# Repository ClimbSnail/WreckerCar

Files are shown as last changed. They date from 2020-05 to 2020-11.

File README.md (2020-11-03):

## 机械臂清障车介绍
本作品参加2017年12月中日韩创新工程竞赛，获金奖（大三上参加的）



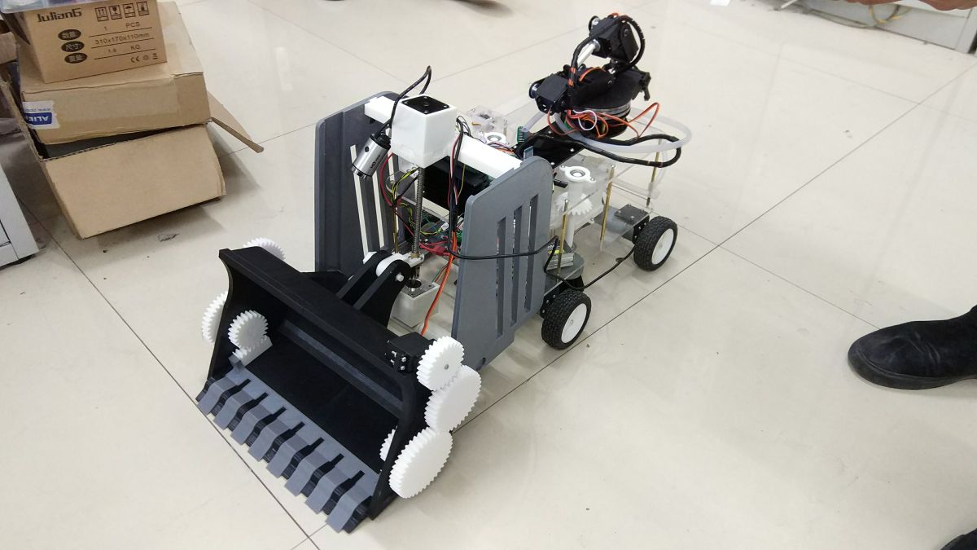
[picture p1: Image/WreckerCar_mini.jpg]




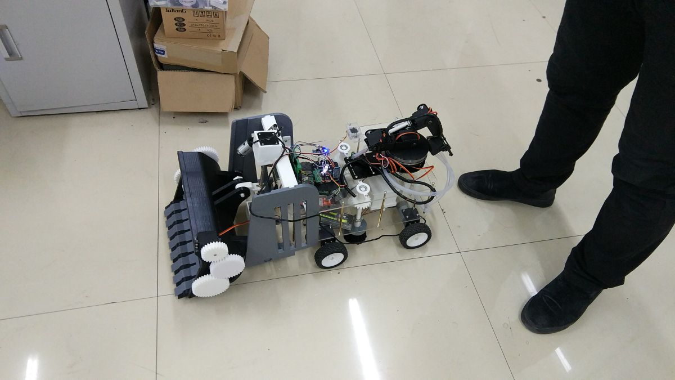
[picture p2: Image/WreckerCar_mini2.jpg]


B站视频[链接](https://b23.tv/BV1qs411L7e6) https://b23.tv/BV1qs411L7e6

如用于学习，可自行去STC官网下载STC12系列的芯片手册。

### 作品简介
1. 电路板:电路图的设计，pcb板的绘制都是由我们自行完成，交由专业厂家打烊，制作成如今的成品。整个作品电源降压、升压部分也特别多，也是一个大工程。

2. 使用价格低廉的51系列主控，对硬件合理的分配及算法的优化，最大程度的挖掘硬件的性能。

3. 控制:使用手机端的app连接机械臂清障车的蓝牙，通过手机蓝牙给控制板发送指令，使之执行特定的动作。

4. 机械臂:使用模拟的六路pwm，并作用独特的联动算法，所有舵机的角度由程序自动计算然后分配，无需人工，使得控制机械臂的时候变得十分简单。

5. 主控控制步进升降:为了增强步进电机的扭力，使用了步进电机驱动器。主控芯片给步进电机驱动器一定的脉冲，从而使信号放大驱动步进电机。

6. 车轮:使用pwm信号并使用光耦隔离驱动多mos管输出大电流以保证底盘四个555电机的正常工作。程序中内置加速减速控制，可实时调车速，保证不同路况的安全运行。使用左右轮差速的方案使得车体在最小的空间中也能完成转向。

7. 水泵和扫帚:使用类似车轮的控制mos管的方案驱动水泵或减速电机。（可调速控制）

8. 车体测边的垃圾箱:使用一个舵机控制车体侧边的垃圾箱收放。

9. 铲斗使用一个舵机完成前后来回铲。

10. 红外功能:为保证安全，车前装有一个红外传感器，当前方有墙之类的障碍使系统自动让车体制动，避免发生意外。

11. LED灯:为适应清障车夜间工作，额外添加了大功率led灯，此led可以实时调整亮度。

12. 远程图像回传摄像头:通过对普通路由器的改装，并刷入基于linux系统的openwrt系统，使日常电脑用的摄像头能够连接路由器，并且使用电脑或者手机浏览器登入查看实时监控。（登入地址http://192.168.1.1:8080/?action=stream）

#### 文件结构
* WreckerCarPCB_Project _（清障车的电路工程文件 AD17绘制）_
* WreckerCar_Code _（清障车的51控制代码 MDK5工程）_
* StructuralDraw _（清障车的solidwork2016结构工程）_
* Image _（实物图片）_
* 多功能消防清障车说明书.doc _（中日韩2017比赛时提交的作品说明书）_
	
#### PCB 3D预览图



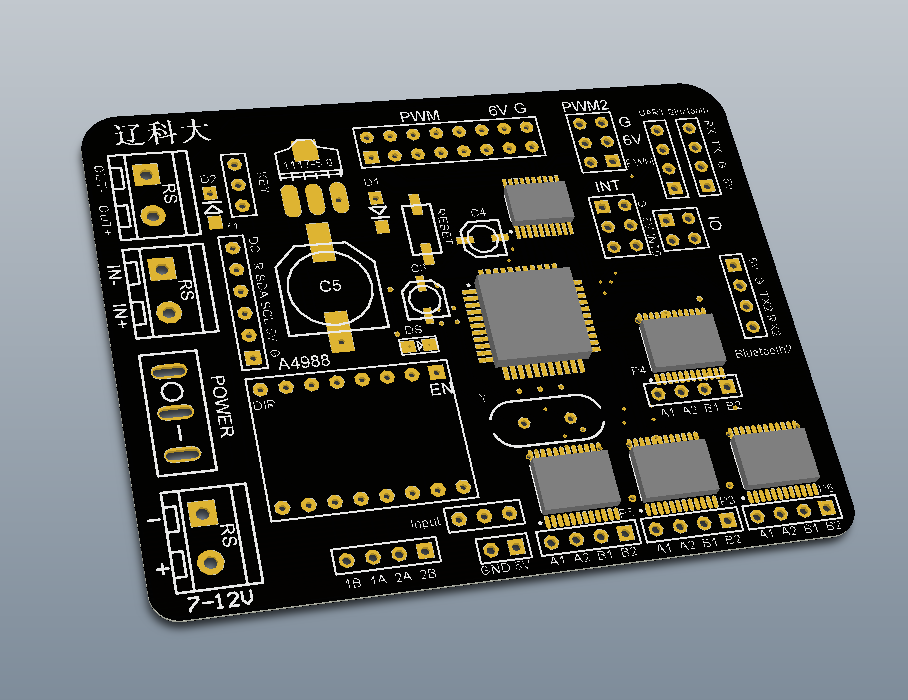
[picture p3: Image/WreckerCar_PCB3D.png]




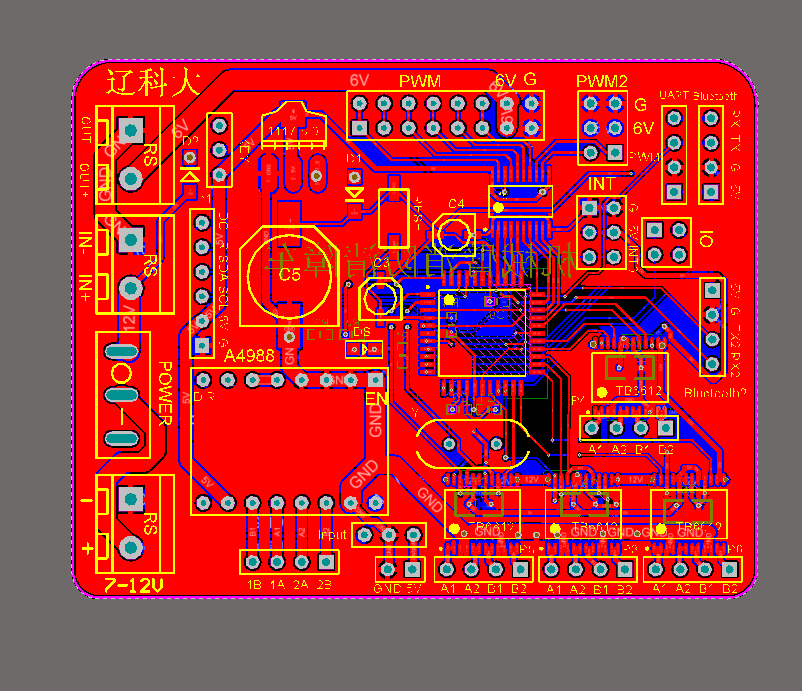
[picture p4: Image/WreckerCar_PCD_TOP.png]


#### 电路存在的问题
	1. 车轮使用的是四个555电机，TB6612不足以驱动（一片TB6612驱一个555时供电不到3s TB6612烧炸）
	2. 由于电机驱动问题，最后另外买了网上现成的驱动板（不用板载的TB6612驱动）。
	3. 铲斗用的步进驱动从原来的A4988改为了TB6600驱动器。

#### 关于代码问题
	1. 之前预计着添加OLED屏幕，调试的过程中烧坏了，最终决定舍弃。

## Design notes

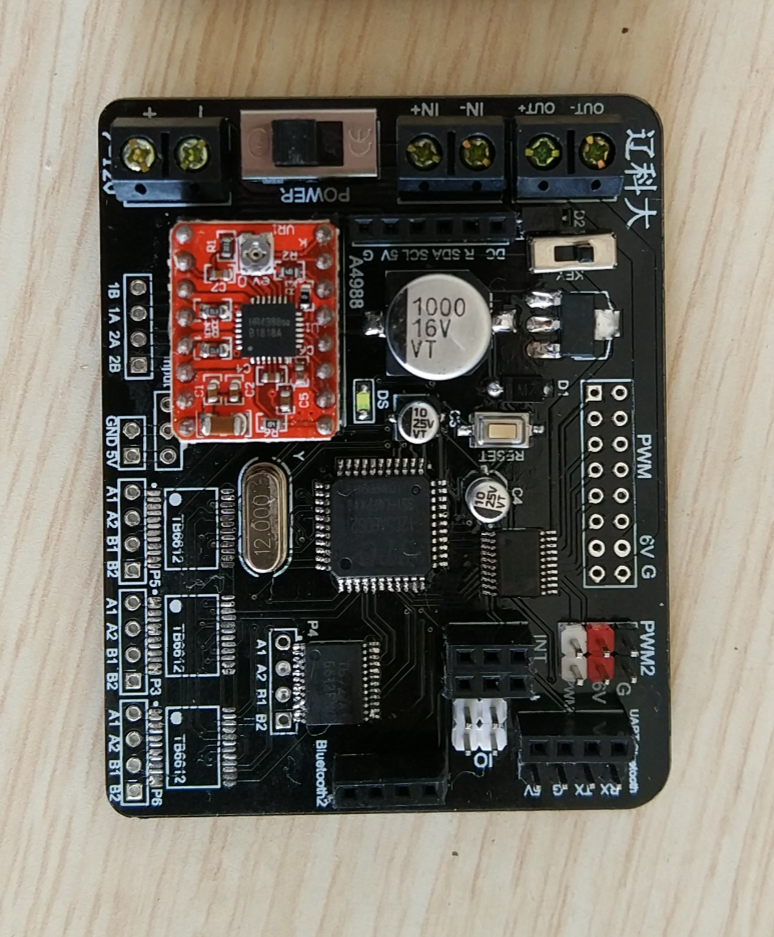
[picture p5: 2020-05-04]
Image/QQ截图20171221224418.png

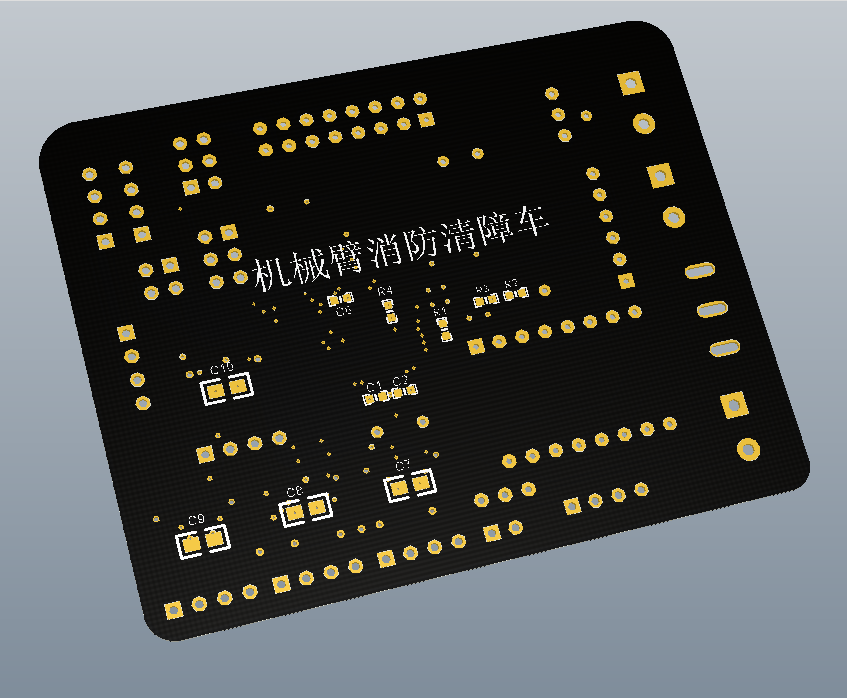
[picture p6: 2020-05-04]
Image/WreckerCar_PCB3D_R.png

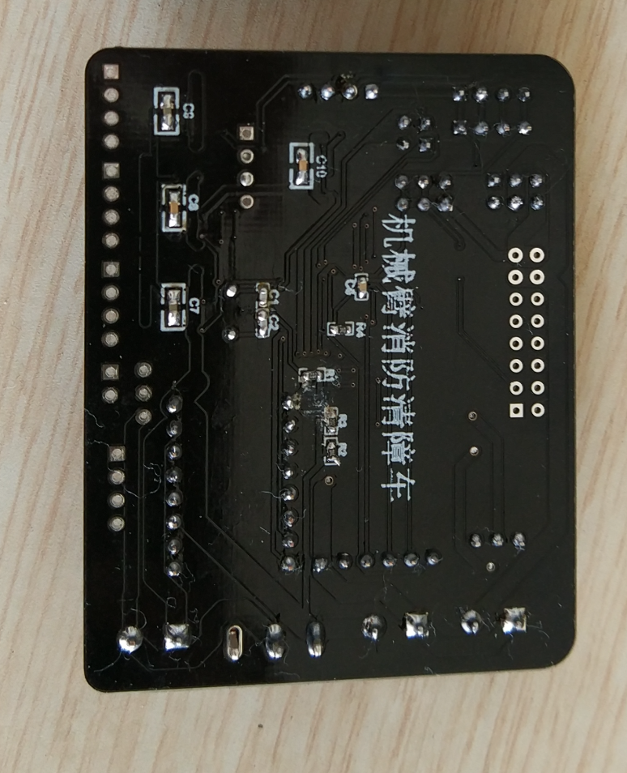
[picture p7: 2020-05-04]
Image/QQ截图20171221224447.png

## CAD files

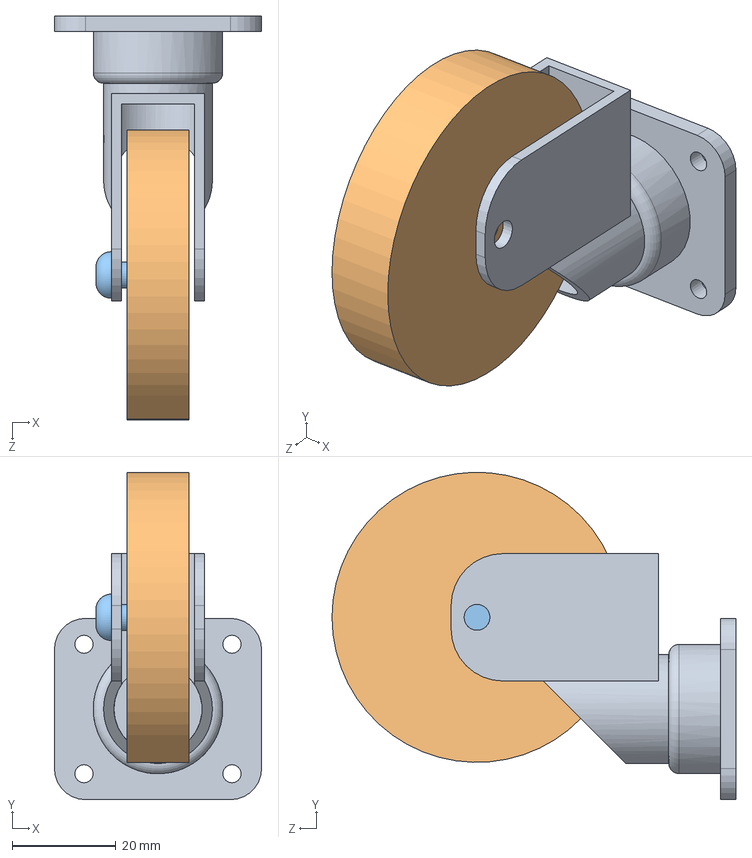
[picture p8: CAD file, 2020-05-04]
StructuralDraw/万向轮/装体123.SLDASM
40.0 x 63.2 x 78.0 mm

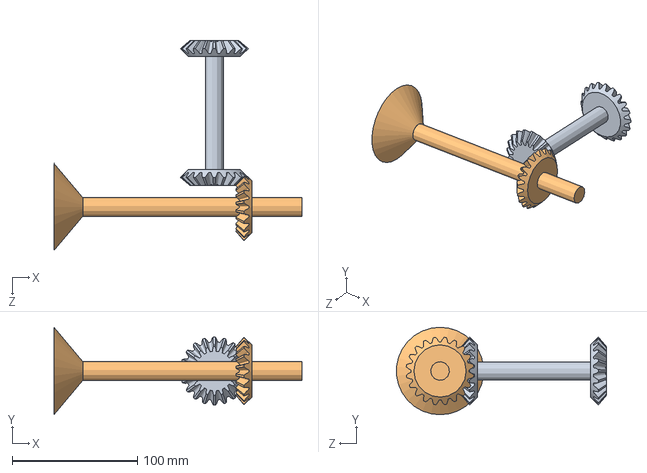
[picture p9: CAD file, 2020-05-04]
StructuralDraw/清洁机构/锥齿轮装配.SLDASM
198.0 x 69.8 x 167.6 mm
锥齿轮01
清洁杆

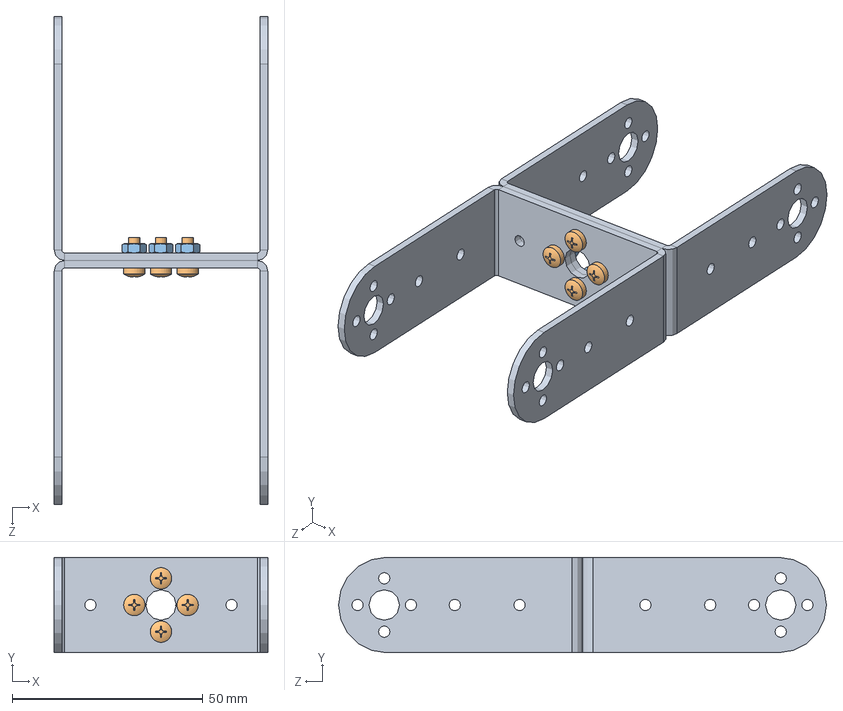
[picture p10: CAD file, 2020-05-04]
StructuralDraw/简易机械臂新底板/长臂组合.SLDASM
56.0 x 25.0 x 128.0 mm
JXS005 x 2
GB818-M3X8-ZN-4.8 x 4
GB6170-M3-ZN-10 x 4

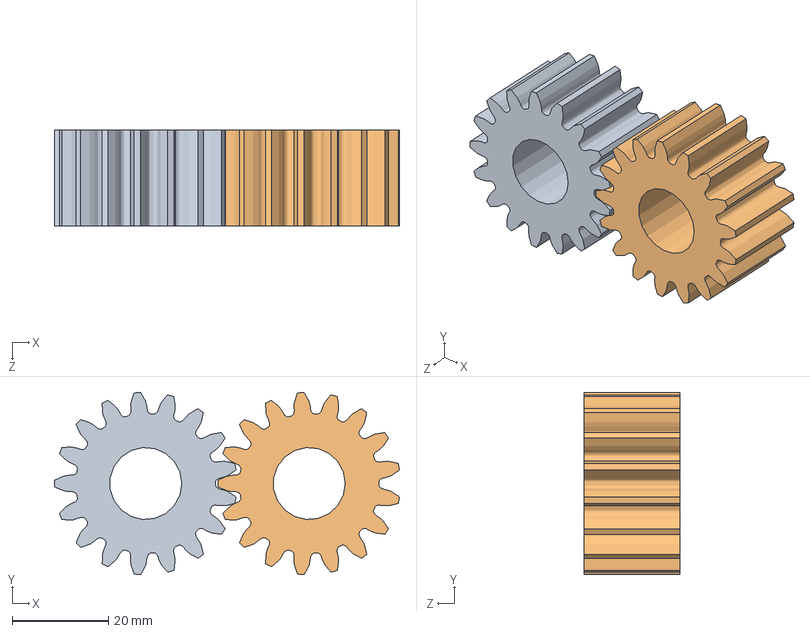
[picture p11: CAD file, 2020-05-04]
StructuralDraw/清洁机构/直齿轮装配01.SLDASM
71.8 x 37.9 x 20.0 mm
小直齿轮
大直齿轮

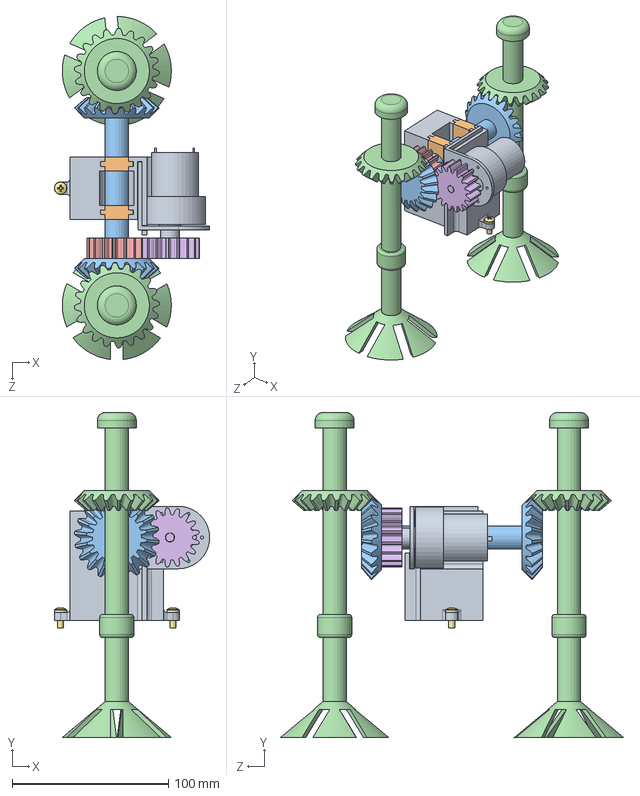
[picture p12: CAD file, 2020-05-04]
StructuralDraw/清洁机构/清洁机构.SLDASM
99.4 x 208.0 x 219.6 mm
电机支架
电机支架销 x 2
锥齿轮01
清洁杆 x 2
小直齿轮
大直齿轮

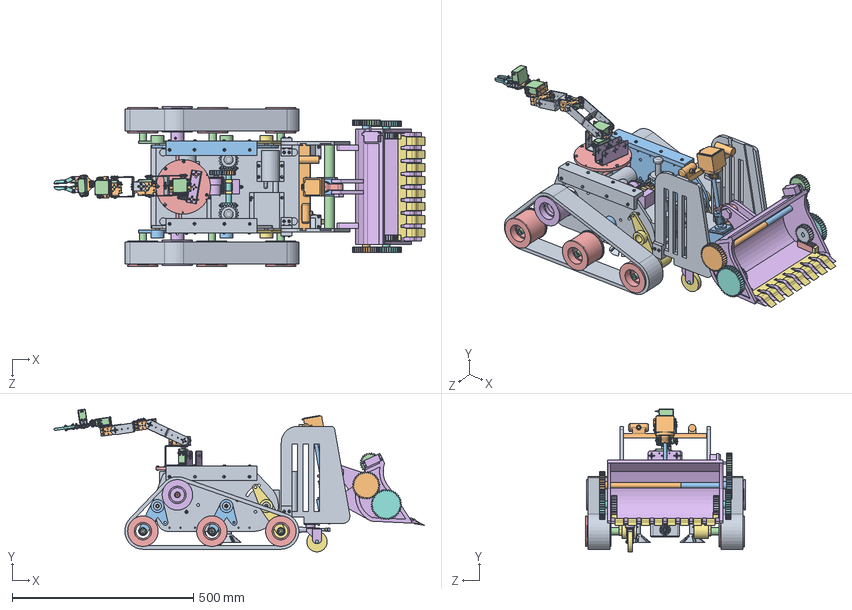
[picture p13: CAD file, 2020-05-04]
StructuralDraw/智能清障小车.SLDASM
1022.5 x 393.3 x 440.0 mm
车身
前电机支架
电机盒
定位筒 x 2
铲斗连杆
铲斗
铲齿
齿轮1 x 2
齿轮2 x 2
齿轮3
齿轮5
齿轮4
齿条 x 2
电机支架
电机支架销 x 2
锥齿轮01
清洁杆 x 2
小直齿轮
大直齿轮
JXS008
GB818-M3X10-ZN-4.8 x 10
GB6170-M3-ZN-10 x 32
JXS005 x 4
JXS006 x 5
GB818-M3X8-ZN-4.8 x 26
杯士轴承 x 4
小舵机 x 6
金属舵盘 x 8
GB818-M4X10-4.8 x 20
GB6170-M4-ZN-10 x 20
GB818-M3X6-ZN-4.8 x 32
JXS007
手爪 （新）
安装扣 x 2
小垫片 x 3
爪子齿轮 2
爪子齿轮
小横杆 x 2
长杆 x 2
螺柱 x 4
GB6170-M3（自锁） x 9
GB818-M3X14-ZN-4.8 x 6
GB818-M3X12-ZN-4.8
DIBAN
履带侧板0
从动轮架轴 x 3
从动轮架 x 2
从动轮轴 x 6
从动轮40 x 6
主动轮40 x 2
从动轮架反 x 2
拉簧销
一号履带 x 2
垫片4.1-10-4 x 2
履带侧板
从动轮架R x 2
侧板支撑轴
从动轮架轴-內螺纹 x 2

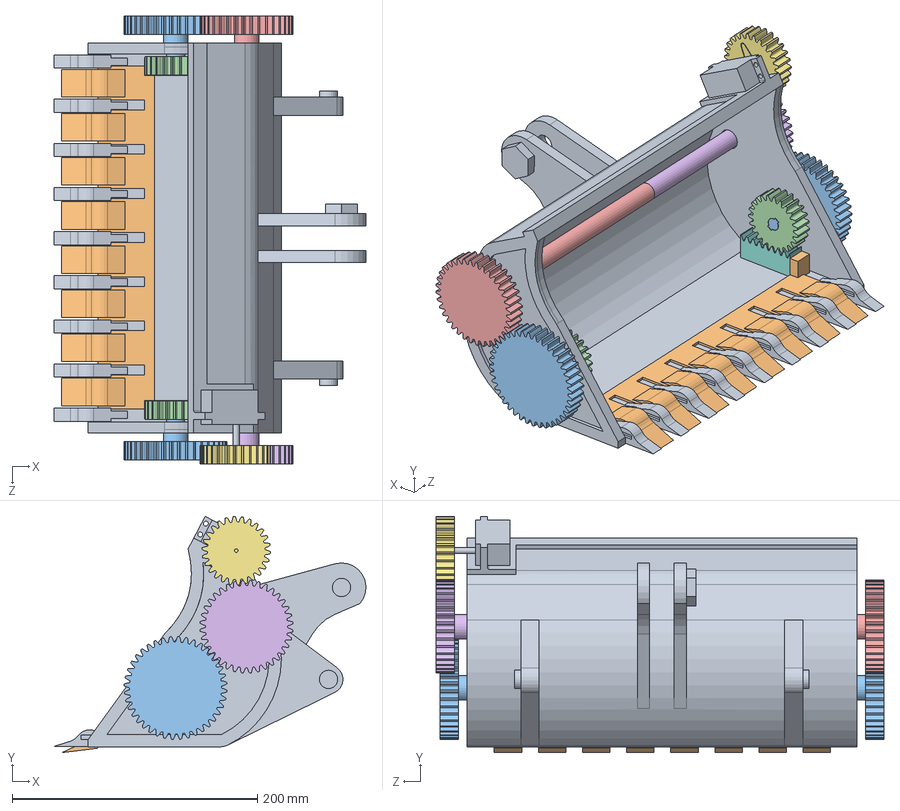
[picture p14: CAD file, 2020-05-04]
StructuralDraw/铲齿机构/铲齿装配.SLDASM
254.5 x 192.8 x 365.0 mm
铲斗
铲齿
齿轮1 x 2
齿轮2 x 2
齿轮3
齿轮5
齿轮4
齿条 x 2

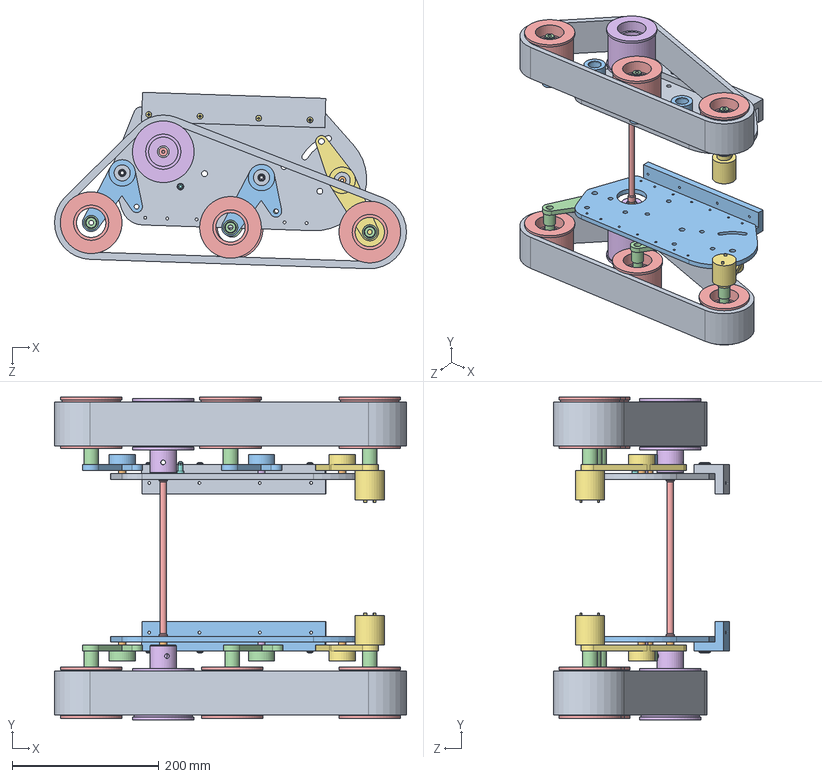
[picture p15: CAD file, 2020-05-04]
StructuralDraw/履带底盘/履带装配体.SLDASM
479.8 x 440.0 x 240.4 mm
履带侧板0
从动轮架轴 x 3
从动轮架 x 2
从动轮轴 x 6
从动轮40 x 6
主动轮40 x 2
从动轮架反 x 2
拉簧销
一号履带 x 2
垫片4.1-10-4 x 2
履带侧板
从动轮架R x 2
侧板支撑轴
从动轮架轴-內螺纹 x 2

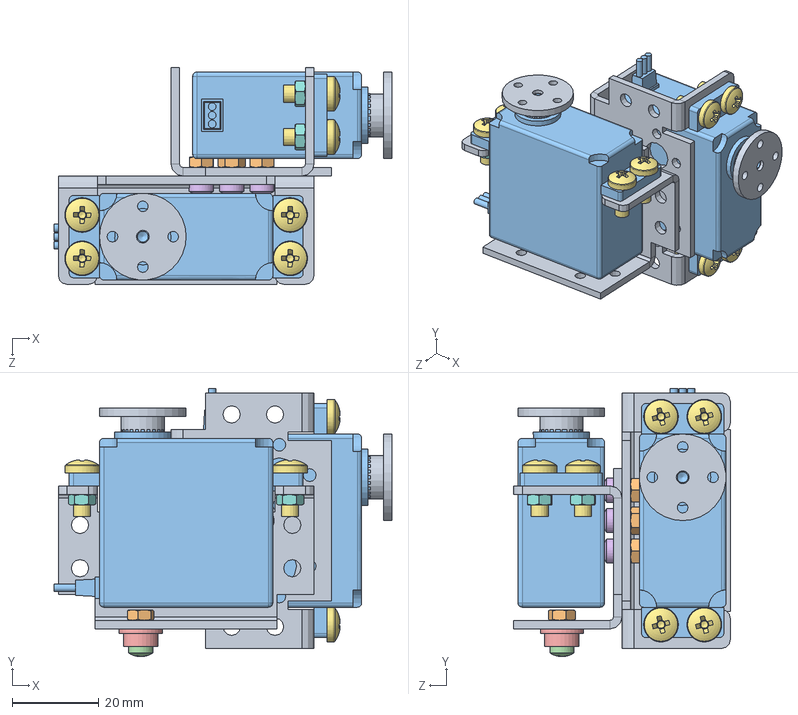
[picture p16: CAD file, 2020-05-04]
StructuralDraw/简易机械臂新底板/手腕组合（新）.SLDASM
78.0 x 61.9 x 50.0 mm
JXS006 x 2
GB6170-M3-ZN-10 x 5
小舵机 x 2
GB818-M3X8-ZN-4.8
杯士轴承
GB818-M3X6-ZN-4.8 x 4
GB818-M4X10-4.8 x 8
GB6170-M4-ZN-10 x 8
金属舵盘 x 2

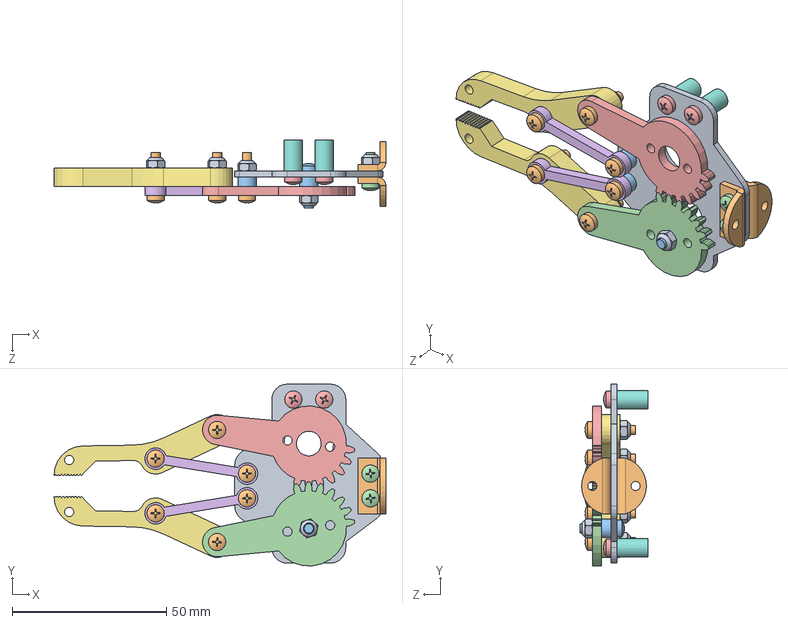
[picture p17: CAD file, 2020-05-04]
StructuralDraw/履带底盘/简易机械臂新底板/爪子（配合）.SLDASM
107.5 x 58.9 x 22.0 mm
手爪 （新）
安装扣 x 2
小垫片 x 3
爪子齿轮 2
爪子齿轮
小横杆 x 2
长杆 x 2
螺柱 x 4
GB6170-M3（自锁） x 9
GB818-M3X14-ZN-4.8 x 6
GB818-M3X12-ZN-4.8
GB818-M3X10-ZN-4.8 x 2
GB818-M3X6-ZN-4.8 x 4

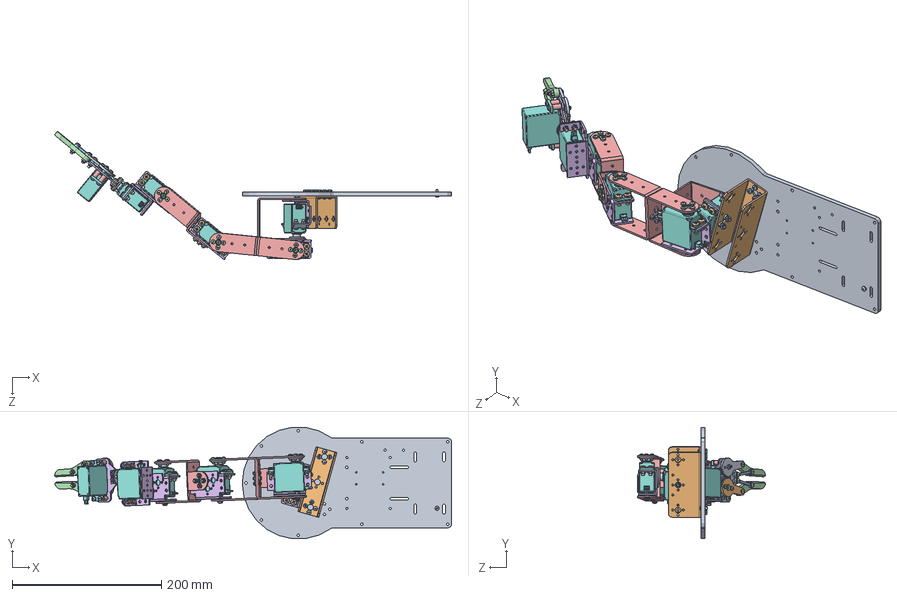
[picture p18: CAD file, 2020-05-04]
StructuralDraw/履带底盘/简易机械臂新底板/新款简易机械臂xg.SLDASM
531.3 x 149.1 x 171.6 mm
JXS008
GB818-M3X10-ZN-4.8 x 10
GB6170-M3-ZN-10 x 32
JXS005 x 4
JXS006 x 5
GB818-M3X8-ZN-4.8 x 26
杯士轴承 x 4
小舵机 x 6
金属舵盘 x 8
GB818-M4X10-4.8 x 20
GB6170-M4-ZN-10 x 20
GB818-M3X6-ZN-4.8 x 32
JXS007
手爪 （新）
安装扣 x 2
小垫片 x 3
爪子齿轮 2
爪子齿轮
小横杆 x 2
长杆 x 2
螺柱 x 4
GB6170-M3（自锁） x 9
GB818-M3X14-ZN-4.8 x 6
GB818-M3X12-ZN-4.8
DIBAN

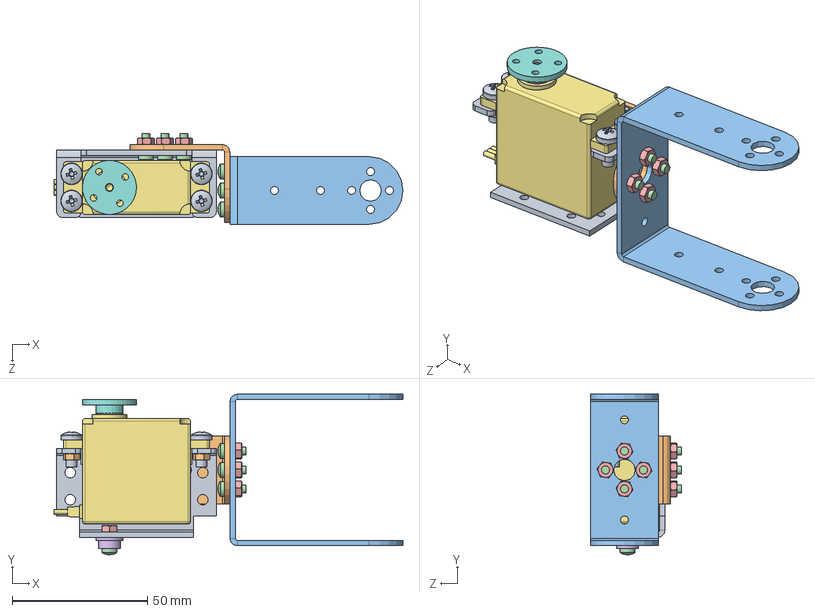
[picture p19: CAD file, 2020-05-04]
StructuralDraw/简易机械臂新底板/小臂组合（新）.SLDASM
129.0 x 59.4 x 33.5 mm
JXS006
JXS007
JXS005
GB818-M3X8-ZN-4.8 x 9
GB6170-M3-ZN-10 x 9
杯士轴承
小舵机
金属舵盘
GB818-M4X10-4.8 x 4
GB6170-M4-ZN-10 x 4

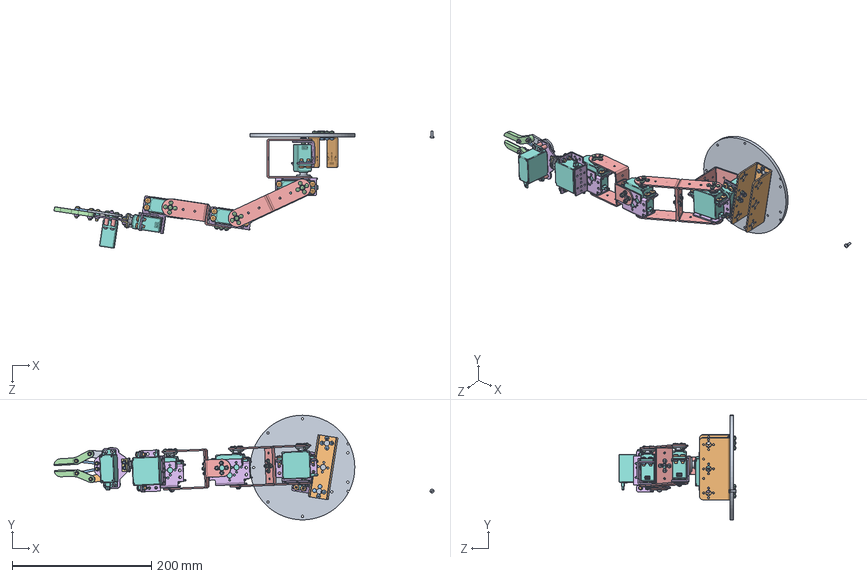
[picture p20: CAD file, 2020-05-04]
StructuralDraw/简易机械臂新底板/新款简易机械臂xg.SLDASM
544.9 x 149.9 x 167.9 mm
JXS008
GB818-M3X10-ZN-4.8 x 10
GB6170-M3-ZN-10 x 32
JXS005 x 4
JXS006 x 5
GB818-M3X8-ZN-4.8 x 26
杯士轴承 x 4
小舵机 x 6
金属舵盘 x 8
GB818-M4X10-4.8 x 20
GB6170-M4-ZN-10 x 20
GB818-M3X6-ZN-4.8 x 32
JXS007
手爪 （新）
安装扣 x 2
小垫片 x 3
爪子齿轮 2
爪子齿轮
小横杆 x 2
长杆 x 2
螺柱 x 4
GB6170-M3（自锁） x 9
GB818-M3X14-ZN-4.8 x 6
GB818-M3X12-ZN-4.8
DIBAN

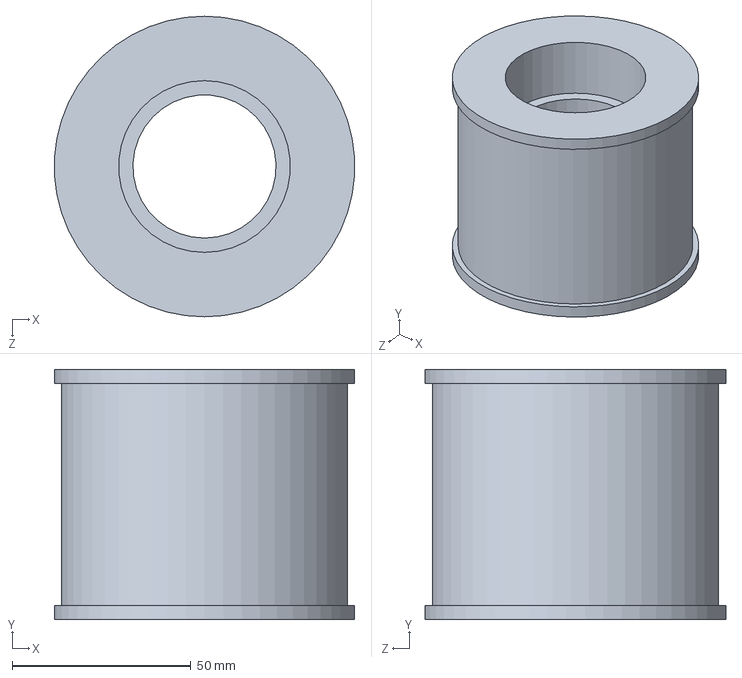
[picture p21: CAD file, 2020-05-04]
StructuralDraw/履带底盘/从动轮40.SLDPRT
83.8 x 70.0 x 84.0 mm

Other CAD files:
StructuralDraw/0000.SLDPRT
StructuralDraw/shuaziliangan.SLDPRT
StructuralDraw/万向轮/111.SLDPRT
StructuralDraw/万向轮/222.SLDPRT
StructuralDraw/万向轮/333.SLDPRT
StructuralDraw/万向轮/轮01.SLDPRT
StructuralDraw/前电机支架.SLDPRT
StructuralDraw/定位筒.SLDPRT
StructuralDraw/履带底盘/一号履带.SLDPRT
StructuralDraw/履带底盘/主动轮40.SLDDRW
StructuralDraw/履带底盘/主动轮40.SLDPRT
StructuralDraw/履带底盘/从动轮40.SLDDRW
StructuralDraw/履带底盘/从动轮架 工程图.SLDDRW
StructuralDraw/履带底盘/从动轮架.SLDPRT
StructuralDraw/履带底盘/从动轮架R 工程图.SLDDRW
StructuralDraw/履带底盘/从动轮架R.SLDPRT
StructuralDraw/履带底盘/从动轮架反 工程图.SLDDRW
StructuralDraw/履带底盘/从动轮架反.SLDPRT
StructuralDraw/履带底盘/从动轮架轴 工程图.SLDDRW
StructuralDraw/履带底盘/从动轮架轴-內螺纹 工程图.SLDDRW
StructuralDraw/履带底盘/从动轮架轴-內螺纹.SLDPRT
StructuralDraw/履带底盘/从动轮架轴.SLDPRT
StructuralDraw/履带底盘/从动轮轴 工程图.SLDDRW
StructuralDraw/履带底盘/从动轮轴.SLDPRT
StructuralDraw/履带底盘/侧板支撑轴 工程图.SLDDRW
StructuralDraw/履带底盘/侧板支撑轴.SLDPRT
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

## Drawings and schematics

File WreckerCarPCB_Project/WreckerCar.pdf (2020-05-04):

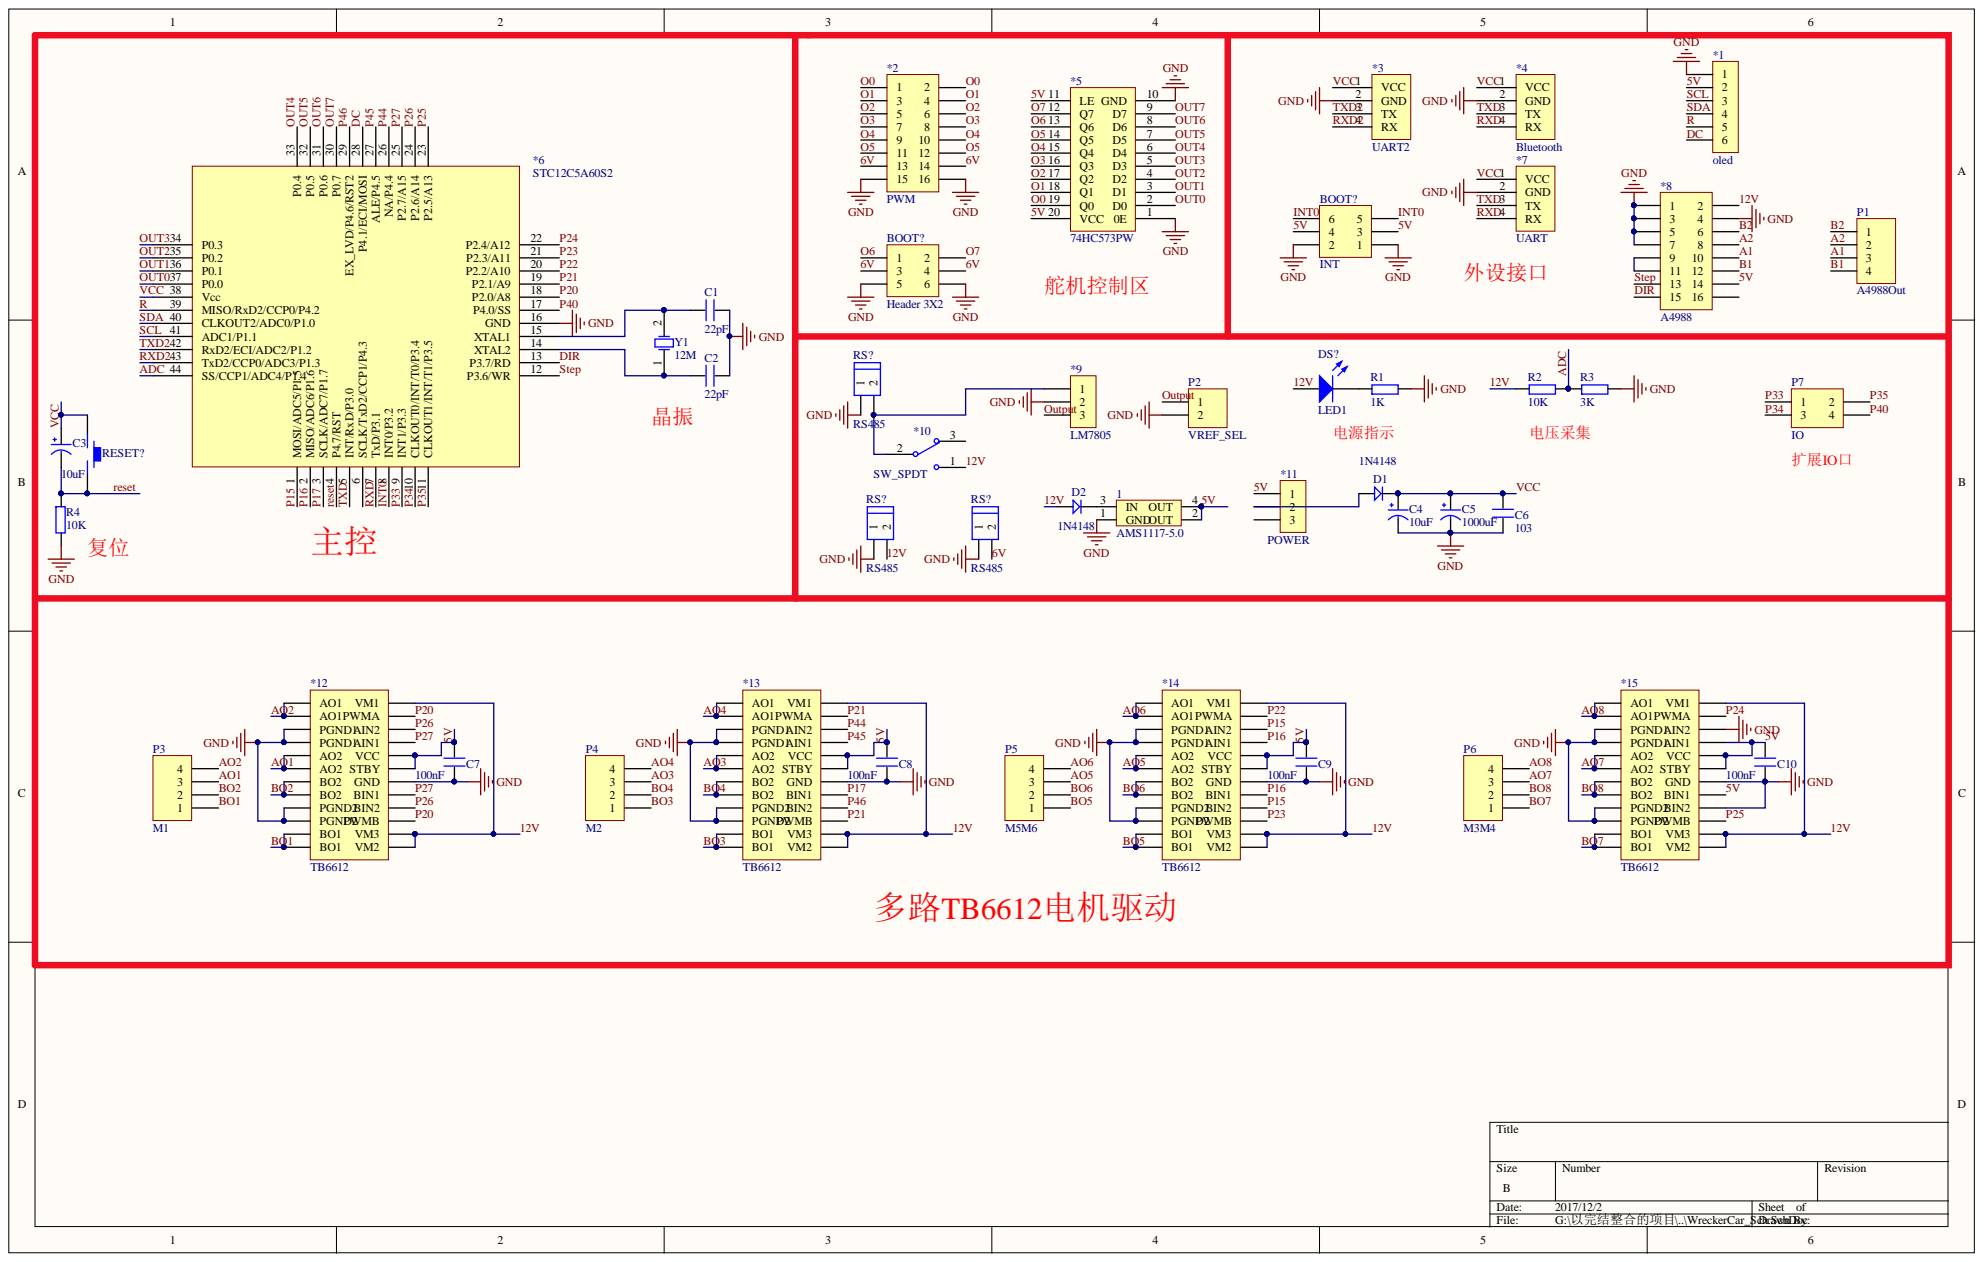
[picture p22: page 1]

P2.5/A13 23 P2.6/A14 24 P2.7/A15 25 NA/P4.4 26 ALE/P4.5 27 P4.1/ECI/MOSI 28 EX_LVD/P4.6/RST2 29 P0.7 30 P0.6 31 P0.5 32 P0.4 33

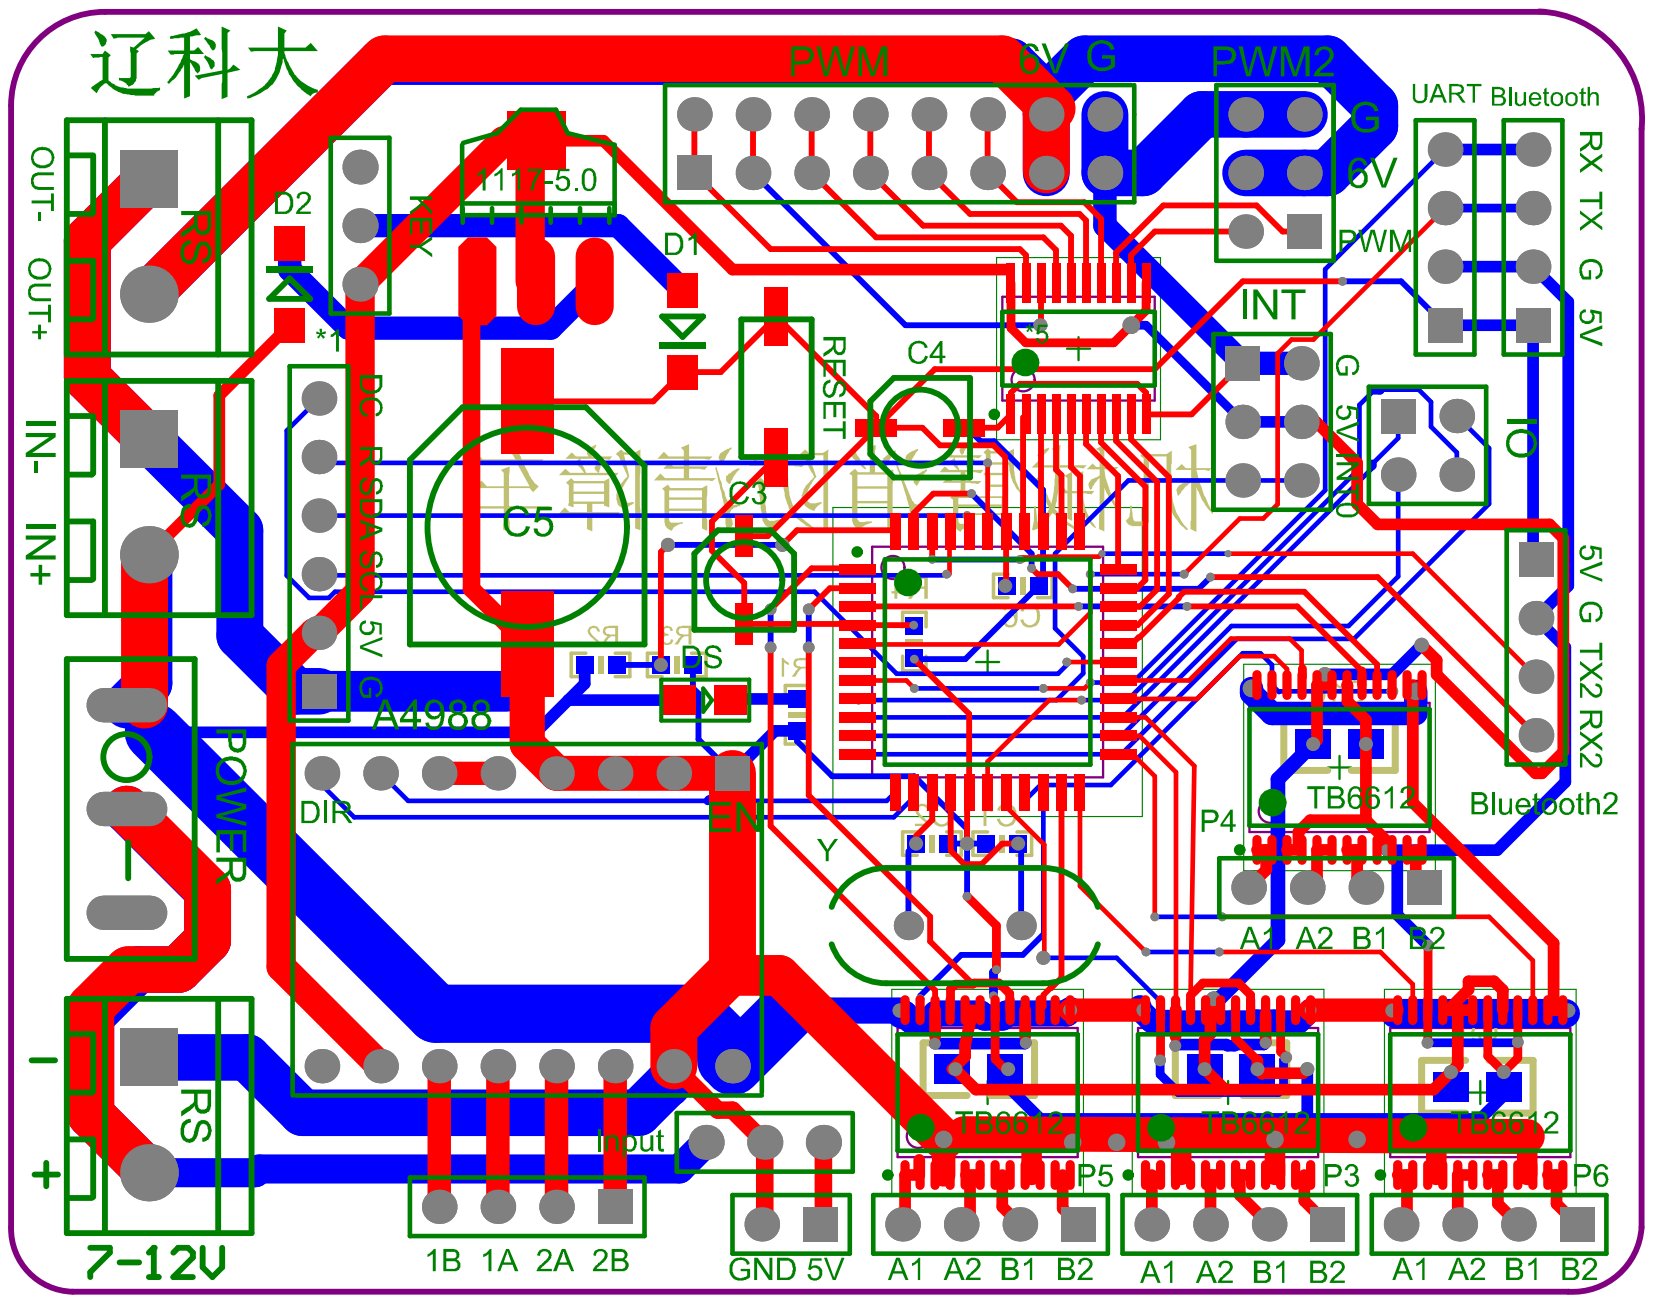
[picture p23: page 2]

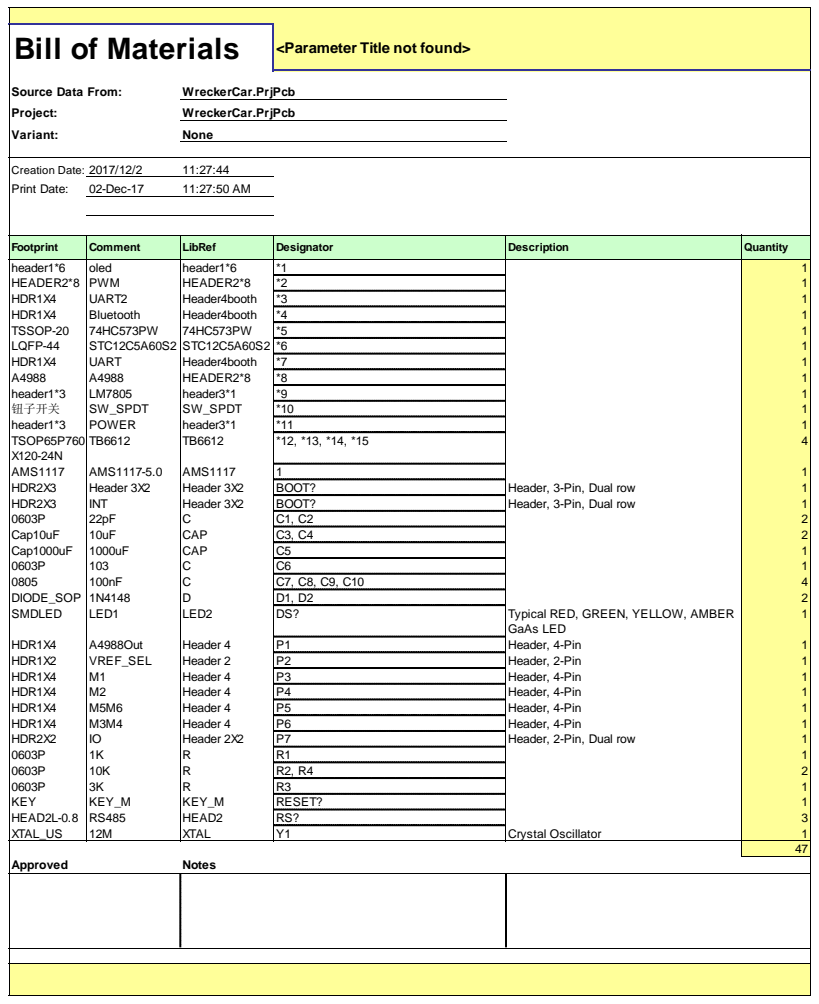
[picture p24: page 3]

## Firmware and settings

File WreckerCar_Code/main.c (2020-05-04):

#include "60s2.h"
#include "timer.h"
#include "uart.h"
#include "uart2.h"
#include "delay.h"
#include "external.h"
#include "math.h"
#include "action.h"
#include "oled.h"
#include "A4988.h"
#include "TB6612.h"

#define uchar unsigned char
#define uint  unsigned int

char FruitFall = 0;
char count = 0;//采摘水果的计数值
int temp;
uchar message = 0x00; //消息
uchar receiveFlag = 0x00;//接收标志
bit busy;
uchar dat[4]= {0,0x80,0x80,0};	//Camera接收的缓冲区
uchar dat_pos = 0;	  //串口2数据缓冲器
uchar uart2flag = 0;  //串口2接收标志
//uchar CameraStatus = 0;	  //摄像头开启标志
//uchar TCameraStatus = 0;  //摄像头使能状态标志记录
uchar BluetoothLink = 0;	//蓝牙连接标志 蓝牙连接时会发送一串"乱码" 设置标志位用来消除
uchar brightness = 0;
int pwm2;
int pwm3;

float x=100,z=150;//实际坐标点

void Uart2() interrupt 8 using 1
{
    if (S2CON & S2RI)
    {
        S2CON &= ~S2RI;     //Clear receive interrupt flag
        dat[dat_pos] = S2BUF;
//		S2BUF = dat[dat_pos];
        if( dat[dat_pos] == 0xff )
            dat_pos = 1;
        else
        {
            dat_pos++;
            if( dat_pos == 4 )
                uart2flag = 1;
            dat_pos %= 4;
        }
    }
    if (S2CON & S2TI)
    {
        S2CON &= ~S2TI;     //Clear transmit interrupt flag
        busy = 0;           //Clear transmit busy flag
    }
}
void uart(void) interrupt 4
{
    if( RI )
    {
        RI = 0;	 //接收位清零
        receiveFlag = 1;//接收标志位置1
        message = SBUF;	//接收信息
				if( message == 0xff )		//蓝牙连接时会发送一串"乱码" 设置标志位用来消除
				{
					BluetoothLink = !BluetoothLink;
					Stop();//车轮停止
					StopWater();//停止抽水
					set_circle_pwm7(0);//关闭pwm7循环转
					StopClean();//停止清洁
					SetLed(0);//关灯
				}

//以下程序测试用
//		SBUF = message;
//		while(!TI);		  //等待发送数据完成
//		TI=0;			  //清除发送完成标志位
    }
}

void Camera_RECEIVE()//摄像头信息处理程序
{
    
}
void RECEIVE_JUGE( )//蓝牙信息处理程序
{
	if( BluetoothLink )//蓝牙连接时会发送一串"乱码" 设置标志位用来消除
	{
    if( receiveFlag == 1 )
    {
        switch( message )
        {
        case 0x00:         
            receiveFlag = 0;
						Stop();
            break;
        case 0x01://向前
            if( x*x+z*z<=58000 && x<240 && z>0)
            {
                if( x*x+z*z>=55000 && z>=0.5f)
                    z -= 0.5f;
                x += 0.5f;
                Change_angle(x,z);
            }
            else if( x*x+z*z>58000 && z>0 )
                x-=0.5f;
            else if( z<=0)
            {
                z+=0.1f;
								pwm2 = 2300+z*10;
								pwm3 = 2000+z*10;
								pwm_change(2,pwm2);
								pwm_change(3,pwm3);
								pwm_change(4,2300);
            }
//			Delay200us();
            break;
        case 0x02://向后
            if( x*x+z*z>=32000 && x>5 && z>0)
            {
                if( x*x+z*z<=33000 && z<240 )
                    z += 0.5f;
                x-=0.5f;
                Change_angle(x,z);
            }
            else if( x*x+z*z>=32000 && z>0 )
                x+=0.5f;
						else if( z <= 0 )
						{
								z-=0.1f;
								pwm2 = 2300+z*10;
								pwm3 = 2000+z*10;
								pwm_change(2,pwm2);
								pwm_change(3,pwm3);
								pwm_change(4,2300);
						}
//			Delay200us();
            break;
        case 0x03://向上
            if( z>0 )
            {
                if( x*x+z*z<58000 )
                {
                    if( x*x+z*z>=55000 && x>5 )
                        x-=0.5f;
                    z+=0.5f;
                    Change_angle(x,z);
                }
                else if( x*x+z*z>=58000 )
                {
                    z-=0.5f;
                }
            }
            else
							{
								z+=0.1f;
								pwm2 = 2300+z*10;
								pwm3 = 2000+z*10;
								pwm_change(2,pwm2);
								pwm_change(3,pwm3);
								pwm_change(4,2300);
							}
//			Delay200us();
            break;
        case 0x04://向下
            if( z>0 )
            {
                if( x*x+z*z>=32000 )
                {
                    if( x*x+z*z<=33000 && x<240)
                        x+=0.5f;
                    z-=0.5f;
                    Change_angle(x,z);
                }
            }
            else
							{
								z-=0.1f;
								pwm2 = 2300+z*10;
								pwm3 = 2000+z*10;
								pwm_change(2,pwm2);
								pwm_change(3,pwm3);
								pwm_change(4,2300);
							}
//			Delay200us();
            break;
        case 0x05:
            temp = 	getSteering(5);
            if(temp>=2497)pwm_change(5,2497); //逆时针
						else
							pwm_change(5,temp+1);
            updata_TimingLeft();
            Delay1ms();
            break;
        case 0x06:
            temp = 	getSteering(5);
            if(temp<=503)pwm_change(5,503); //顺时针
						else
							pwm_change(5,temp-1);
            updata_TimingLeft();
            Delay1ms();
            break;
        case 0x07:
            temp = 	getSteering(0);
            if(temp>=1600)pwm_change(0,1600); //夹紧
						else
							pwm_change(0,temp+1);
            updata_TimingLeft();
            Delay1ms();
            break;
        case 0x08:
            temp = 	getSteering(0);
            if(temp<=900)
							pwm_change(0,900); //松开
						else
						pwm_change(0,temp-1);
            updata_TimingLeft();
            Delay1ms();
            break;
        case 0x09://前进
						Forward();
            Delay100ms();
            break;
        case 0x0a://后退
						Back();
            Delay100ms();
            break;
        case 0x0b://顺拐
						Turnrigth();
            Delay100ms();
            break;
        case 0x0c://逆拐
						Turnleft();
            Delay100ms();
            break;
        case 0x0d://打开水泵
            StartWater();
            break;
        case 0x0e://关闭水泵
            StopWater();
            break;
        case 0x0f://开始清洁
						StartClean();
            break;
        case 0x10://停止清洁
						StopClean();
            break;
        case 0x11:
            SetPulsePositive(1000);//铲斗向上
						receiveFlag = 0;
						break;
        case 0x12:
            SetPulseReverse(1000);//铲斗向下
						receiveFlag = 0;
						break;
				case 0x13:
						set_circle_pwm7(1);//启用pwm7循环转
						receiveFlag = 0;
						break;
				case 0x14:
						set_circle_pwm7(0);//关闭pwm7循环转
						receiveFlag = 0;
						break;
				case 0x15://开垃圾箱
						open_Dustbin(1);//开关垃圾箱 1为启用 0为关闭
						receiveFlag = 0;
						break;
				case 0x16://关垃圾箱
						open_Dustbin(0);//开关垃圾箱 1为启用 0为关闭
						receiveFlag = 0;
						break;
				case 0x17://Led增量一个单位
						if( brightness == 1 )
							brightness = 1;
						else
							brightness = (brightness+10-1)%10;
						SetLed(brightness);//num为0时关闭 开启的值为1-9,1最大 9最小
						receiveFlag = 0;
						break;
				case 0x18://Led减小一个单位
						if( brightness == 0 )
							brightness = 0;
						else
							brightness = (brightness+1)%10;
						SetLed(brightness);//num为0时关闭 开启的值为1-9,1最大 9最小
						receiveFlag = 0;
						break;
				case 0x19://车速调最高
					SetSpeed(1);//设置速度 值为1-9,1最大 9最小 0时关闭
					break;
				case 0x1A://车速调一半
					SetSpeed(8);//设置速度 值为1-9,1最大 9最小 0时关闭
					break;
        default:
            break;
        }

    }
	}
}


void main()	//主程序
{
		P0 = 0x00;
		P1 = 0x00;
		P2 = 0xff;
		P3 = 0xdf;//步进驱动使能关
    P4SW |= 0x70;	 //启用P4.4 P4.5 P4.6
	
		SetLed(0);//num为0时关闭 开启的值为1-9,1最大
	
//    OLED_Init();
//    OLED_Clear();
//    OLED_ShowCHinese(0,0,9);//辽
//    OLED_ShowCHinese(20,0,10);//宁
//    OLED_ShowCHinese(40,0,5);//科
//    OLED_ShowCHinese(60,0,6);//技
//    OLED_ShowCHinese(80,0,11);//大
//    OLED_ShowCHinese(100,0,12);//学
//    OLED_ShowCHinese(0,4,17);//水
//    OLED_ShowCHinese(14,4,18);//果
//    OLED_ShowCHinese(28,4,19);//采
//    OLED_ShowCHinese(42,4,20);//摘
//    OLED_ShowCHinese(56,4,21);//累
//    OLED_ShowCHinese(70,4,22);//计
//    OLED_ShowChar(84,4,':');
//    OLED_ShowNum(92,4,0,3,16);//显示ASCII字符的码值
		
	  pwm_change(0,900);
		pwm_change(1,1500);
		pwm_change(2,1500-90);
    pwm_change(3,1500-70);
    pwm_change(4,1500);
    updata_TimingLeft();//更新剩余低电平时间
		
//    usart_init();
    uart_init12M(9600); //串口初始化
    timer0_init();//定时器0初始化
		timer1_init();//定时器1初始化
    steering_init();//舵机参数的初始化
//    ext0_init();	//外部中断0初始化
//    ext1_init();	//外部中断1初始化
    while(1)
    {
        RECEIVE_JUGE();  //串口接收判断
    }
}

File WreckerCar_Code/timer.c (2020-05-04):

#include "timer.h"
#include "TB6612.h"

//定时值的高8位与低8位
static uchar timingValueH[9]= {0xFA,0xFA,0xFE,0xFE,0xFC,0xFA,0xFD,0xFB, 0x00};
static uchar timingValueL[9]= {0x24,0x24,0x0C,0x0C,0x18,0x24,0xDA,0xB3, 0x00};
//   0xF6	0x3C

//定时器中使用的定时计数值下标
static uchar pwm_flag0 = 0;
static uint pwm_flag1 = 0;
static uchar pwm7H = 0xFB;
static uchar pwm7L = 0xB3;
uchar pos;

//低电平的剩余时间
static uint timingLeftValue0 = 0;

static uchar pwm;
//P0对应PWM0~7   目前申明都没用上
sbit pwm0 = P0^0;
sbit pwm1 = P0^1;
sbit pwm2 = P0^2;
sbit pwm3 = P0^3;
sbit pwm4 = P0^4;
sbit pwm5 = P0^5;
sbit pwm6 = P0^6;
sbit pwm7 = P0^7;


//定时器0初始化
void timer0_init()
{
    EA = 1;	  //开启总中断
    ET0 = 1;	   // 定时器0可用
    TMOD |= 0x01;//设置定时器0为工作方式1(16位计数器)
    //先初始赋值pwm0
    TH0 = timingValueH[0];
    TL0 = timingValueL[0];
    TR0 = 1;//定时器0开始计数
}
//定时器1初始化
void timer1_init()
{
    EA = 1;	  //开启总中断
    ET1 = 1;	   // 定时器1可用
    TMOD |= 0x10;//设置定时器0为工作方式1(16位计数器)
    //先初始赋值pwm9
    TH1 = timingValueH[8];
    TL1 = timingValueL[8];
    TR1 = 1;//定时器1开始计数
}

//定时器中断0
void timer0 (void) interrupt 1
{

    if( pwm_flag0 == 8 )  //当要执行PWM8时
    {
        P0 = 0x00;
        TH0 = timingValueH[8];
        TL0 = timingValueL[8];
    }
    else				  //定时PWM0~7
    {
        if( pwm_flag0 == 0 )
            P0 = 0x01;
        else
            P0 <<= 1;
        TH0 = timingValueH[pwm_flag0]; //定时时间赋值
        TL0 = timingValueL[pwm_flag0];
    }
    pwm_flag0 = (pwm_flag0+1)%9;	//下标推进
}

//定时器中断1
void timer1 (void) interrupt 3
{
		TH1 = 0xFC;
    TL1 = 0x18;
//		TH1 = 0xF4;
//    TL1 = 0x48;
		pwm_flag1 = (pwm_flag1+1)%2000;
		
		pos = pwm_flag1%10;
		
		if( CAR12Speed == pos )
		{
			CARPwm1 = 1;
		}
		if( CAR34Speed == pos )
		{
			CARPwm2 = 1;
			CARPwm3 = 1;
		}
		if( WaterSpeed == pos )
		{
			WaterPwm = 1;
		}
		if( CleanSpeed == pos )
		{
			CleanPwm = 1;
		}
		if( LedSpeed == pos )
		{
			LEDPwm = 1;
		}
		
		if( pos == 0 )
		{
			CARPwm1 = 0;
			CARPwm2 = 0;
			CARPwm3 = 0;
			WaterPwm = 0;
			CleanPwm = 0;
			LEDPwm = 0;
		}
		
		if( pwm_flag1 == 999)
		{
			timingValueH[7] = 0xFB;
			timingValueL[7] = 0xB3;
			updata_TimingLeft();
		}
		if( pwm_flag1 == 1999)
		{
			timingValueH[7] = pwm7H;
			timingValueL[7] = pwm7L;
			updata_TimingLeft();
		}
}


void pwm_change(uchar pwmNumber,uint pwmDuty)	//pwmNumber范围0~7 pwmDuty(1~2500us)
{
    pwmDuty = 65536-pwmDuty;
//先改变定时时间的值
//	timingValueH[pwmNumber]	=  pwmDuty/256;
//	timingValueL[pwmNumber]	=  pwmDuty%256;
//使用位操作,运算速度更快
    timingValueH[pwmNumber]	=  pwmDuty>>8;
    timingValueL[pwmNumber]	=  (pwmDuty<<8)>>8;

//	if( pwmNumber == 5 )
//		SREET6 = 65536-(timingValueH[5]*256+timingValueL[5]);
//	if( pwmNumber == 0 )
//		SREET1 = 65536-(timingValueH[0]*256+timingValueL[0]);
}

//更新剩余低电平时间
void updata_TimingLeft()
{
    uchar count;
    //计算剩余低电平的剩余时间
    timingLeftValue0 = 65536-20000;
    for( count = 0 ; count<8 ; count++ )
        timingLeftValue0 += ( 65536-(timingValueH[count]*256+timingValueL[count]) );
    timingValueH[8] = timingLeftValue0>>8;	//更新剩余低电平时间
    timingValueL[8] = (timingLeftValue0<<8)>>8;
}

int getSteering(int num)
{
    return 65536-(timingValueH[num]*256+timingValueL[num]);
}


void set_circle_pwm7(uchar num)//启用pwm7循环转 1为启用 0为关闭
{
	if( num )
	{
		pwm7H = 0xF8;
		pwm7L = 0xF7;
	}
	else
	{
		pwm7H = 0xFB;
		pwm7L = 0xB3;
	}
}

void open_Dustbin(uchar num)//开关垃圾箱 1为启用 0为关闭
{
	if( num )//高电平1500us
	{
		timingValueH[6] = 0xFA;
		timingValueL[6] = 0x24;
	}
	else//高电平550us
	{
		timingValueH[6] = 0xFD;
		timingValueL[6] = 0xDA;
	}
}
